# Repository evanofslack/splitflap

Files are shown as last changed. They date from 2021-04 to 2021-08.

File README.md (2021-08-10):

# DIY Split-Flap Display

This is a work in progress DIY [split-flap display](https://en.wikipedia.org/wiki/Split-flap_display). This is a fork of [scottbez1/splitflap](https://github.com/scottbez1/splitflap) where the display housing has been modified to be use 3D printed parts and acrylic panels with the goal of producing a more compact design. By enclosing the stepper motor within the flap housing, the overall footprint of a single unit is reduced. The acrylic panels fully enclose the internal components, leading to a clean and minimal appearance. 



<a href="https://www.youtube.com/watch?v=UAQJJAQSg_g" target="_blank">How a split-flap display works</a>

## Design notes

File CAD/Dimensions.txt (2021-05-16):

"Width"= 64mm

"Height" = 150mm

"Depth"= 90mm

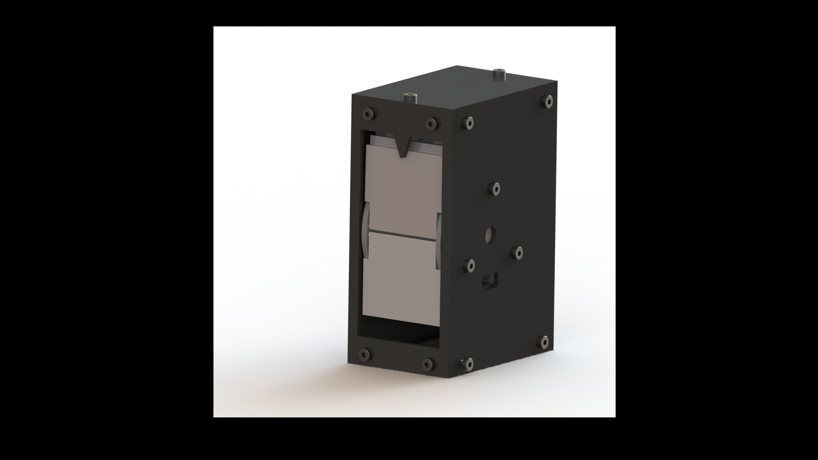
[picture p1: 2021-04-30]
renders/Render2.JPG

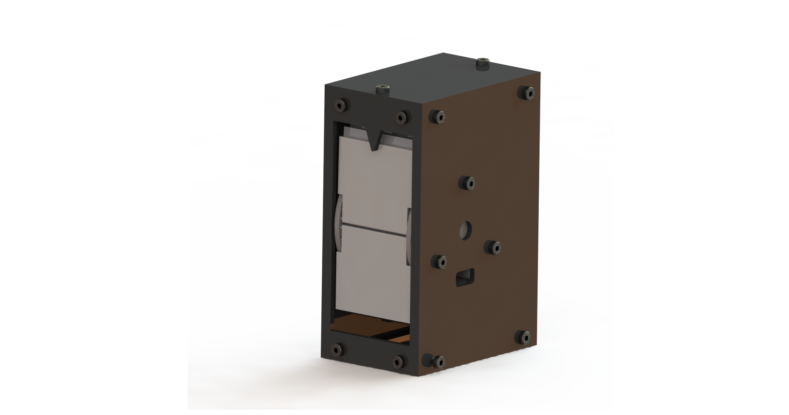
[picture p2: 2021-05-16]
renders/CollapsedRender.png

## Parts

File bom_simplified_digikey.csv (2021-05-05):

Quantity | Digi-Key Part Number | Customer Reference
2 | P5193-ND | C1, C3
1 | BC2665CT-ND | C2
1 | CP-202A-ND | CON1
1 | 732-5010-ND | D1
1 | 732-5008-ND | D2
1 | S1012EC-02-ND | JP1
1 | S9337-ND | JP1
4 | 455-2270-ND | P1, P2, P3, P4
3 | S1012EC-04-ND | P6, P7, P8
4 | S1112EC-03-ND | P100, P100, P100, P100
1 | CF14JT2K20CT-ND | R1
5 | CF14JT47K0CT-ND | R3, R4, R5, R6, R10
1 | CF14JT220RCT-ND | R7
1 | CF14JT470RCT-ND | R9
1 | S1012EC-03-ND | U1
1 | S1012EC-02-ND | U1
1 | S7106-ND | U1
2 | 576-1309-ND | U2, U4
1 | 296-8251-5-ND | U3
1 | 1528-1104-ND | U5, U6, U7, U8
4 | AH3391Q-P-BDI-ND | U100, U100, U100, U100
4 | 469-1027-ND | U100, U100, U100, U100

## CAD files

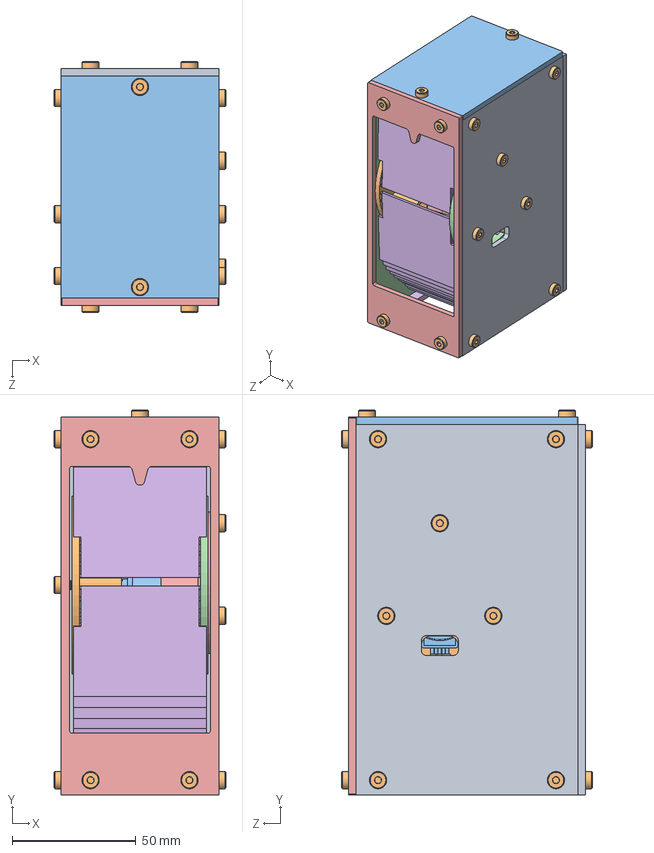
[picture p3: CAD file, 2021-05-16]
CAD/SplitFlapAssembly.SLDASM
69.6 x 155.8 x 101.6 mm
RightPanel
Holder1
Motor_28BYJ-48
Holder2
MotorHolder
Flap x 45
Hall Effect Sensor
LinkageV2
BackPanel
93070A101_LOW-PROFILE SOCKET HEAD CAP SCREW x 22
TopPanel
LeftPanel
FrontPanel
LinkageBottom

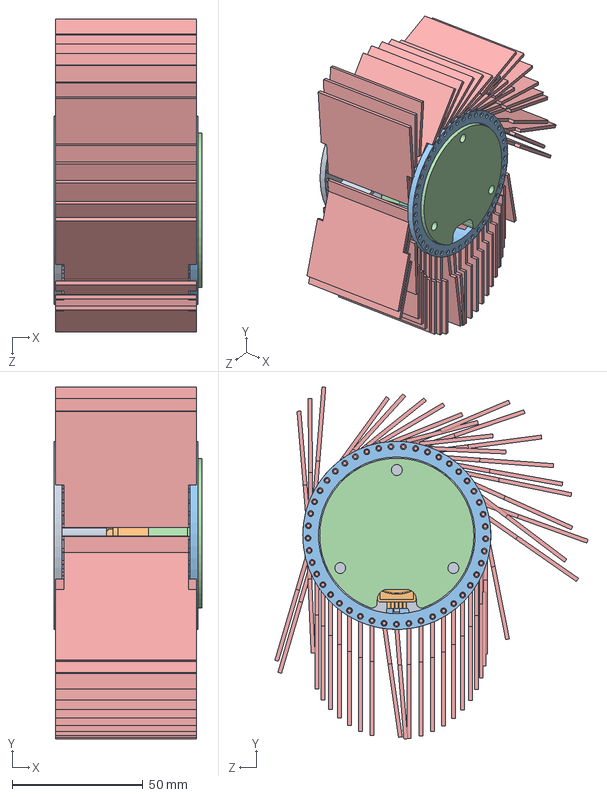
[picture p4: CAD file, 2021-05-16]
CAD/MotorAssembly.SLDASM
56.5 x 134.7 x 119.9 mm
Holder1
Motor_28BYJ-48
Holder2
MotorHolder
Flap x 45
Hall Effect Sensor

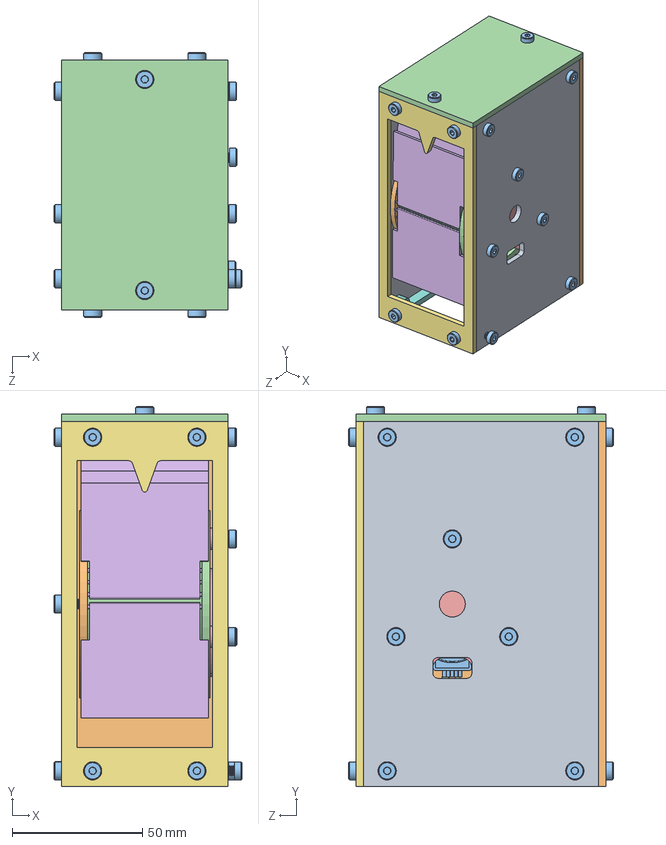
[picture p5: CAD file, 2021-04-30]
CAD/SplitFlapAssemblyExplode.SLDASM
72.1 x 145.8 x 101.6 mm
RightPanel
Holder1
Motor_28BYJ-48
Holder2
MotorHolder
Flap x 12
FrontPanel
LinkageV2 x 2
LeftPanel
BackPanel
93070A101_LOW-PROFILE SOCKET HEAD CAP SCREW x 22
TopPanel

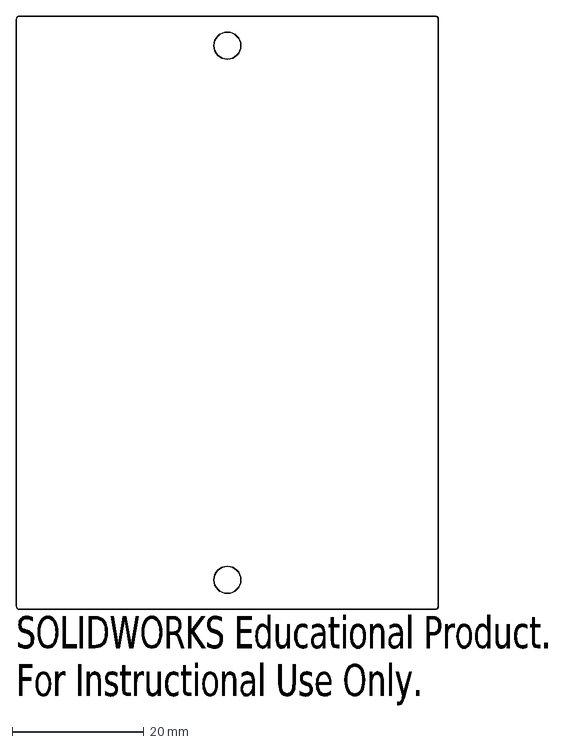
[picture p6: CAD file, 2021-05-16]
CAD/01_Acrylic/DXF/(4x)TopPanel.DXF
SOLIDWORKS Educational Product.
For Instructional Use Only.

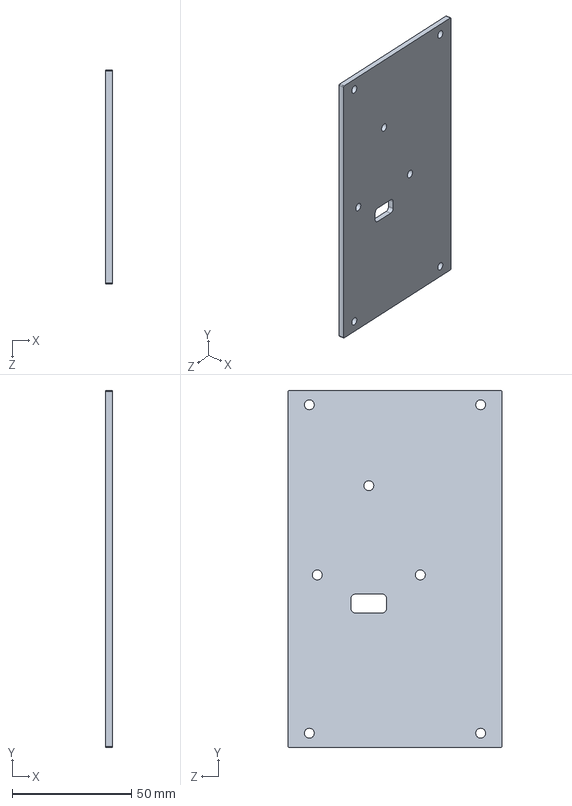
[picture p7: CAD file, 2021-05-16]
CAD/01_Acrylic/RightPanel.SLDPRT
3.00 x 150.0 x 90.0 mm

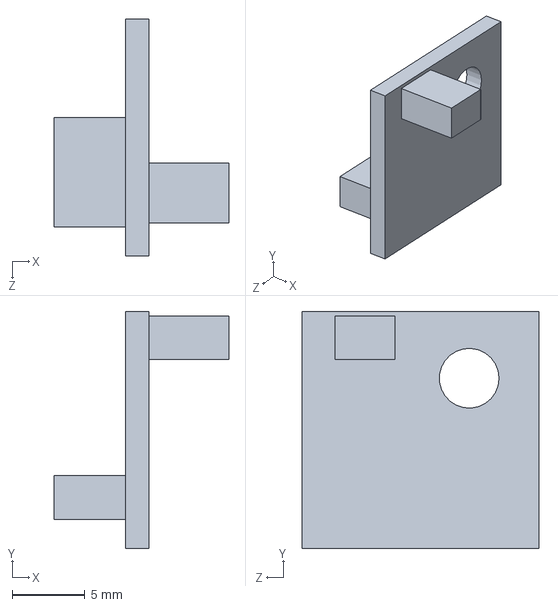
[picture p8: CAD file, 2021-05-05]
CAD/02_OTS/Hall Effect Sensor.SLDPRT
12.0 x 16.3 x 16.3 mm

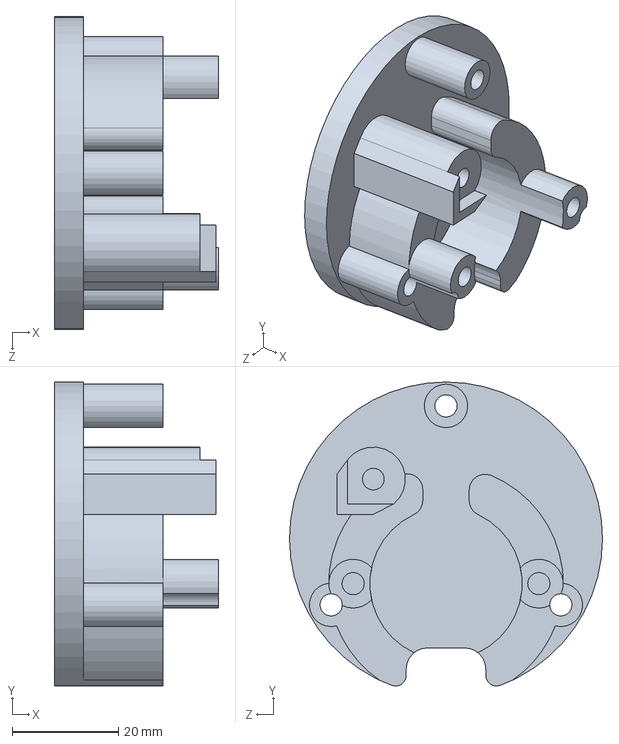
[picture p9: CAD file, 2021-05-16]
CAD/03_3DPrint/MotorHolder.SLDPRT
31.0 x 57.3 x 59.0 mm

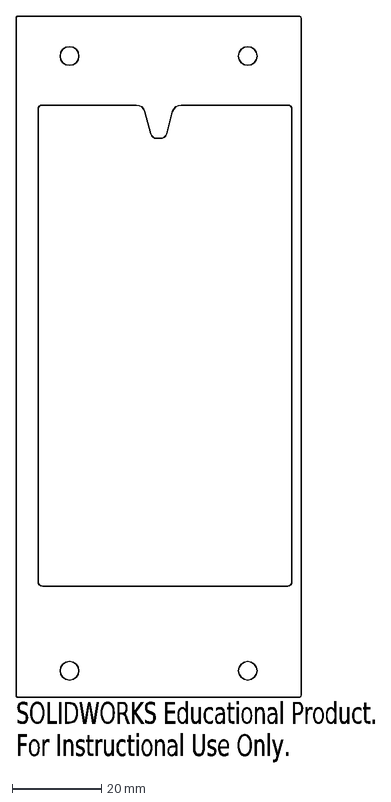
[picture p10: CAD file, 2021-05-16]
CAD/01_Acrylic/DXF/(3x)FrontPanel.DXF
SOLIDWORKS Educational Product.
For Instructional Use Only.

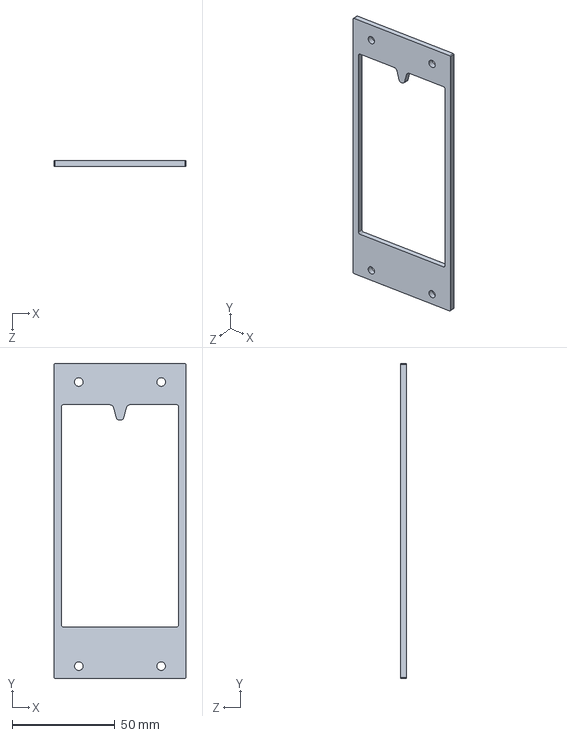
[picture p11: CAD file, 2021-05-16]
CAD/01_Acrylic/FrontPanel.SLDPRT
64.0 x 153.0 x 3.00 mm

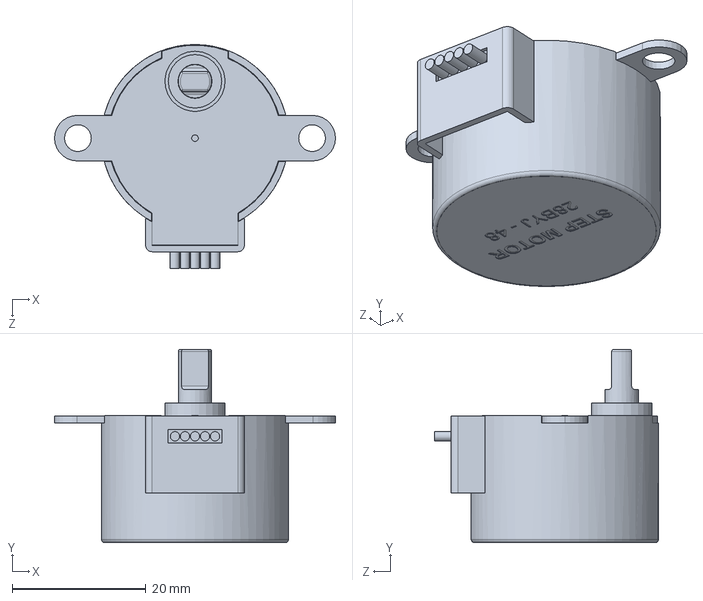
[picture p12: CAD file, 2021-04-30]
CAD/02_OTS/Motor_28BYJ-48.SLDPRT
42.0 x 28.9 x 33.5 mm

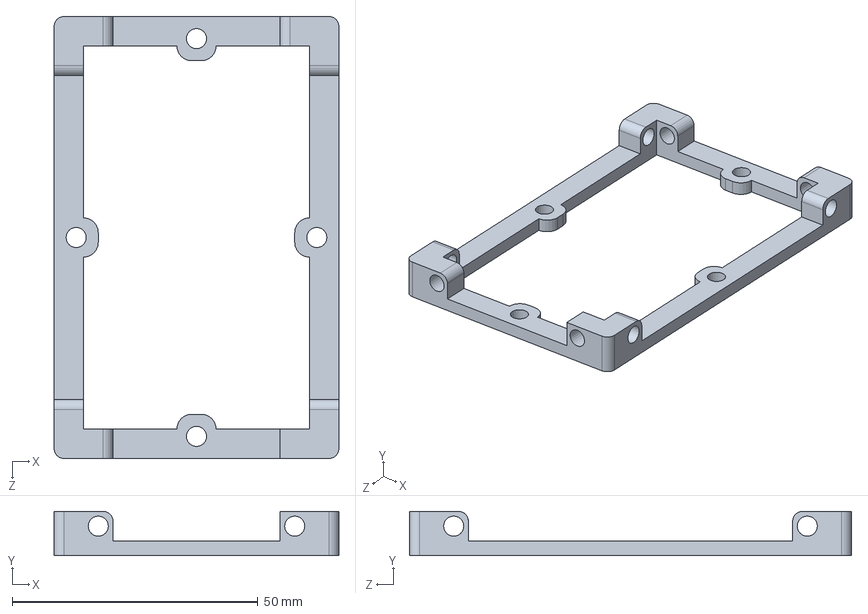
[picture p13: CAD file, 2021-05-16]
CAD/03_3DPrint/LinkageV2.SLDPRT
58.0 x 9.00 x 90.0 mm

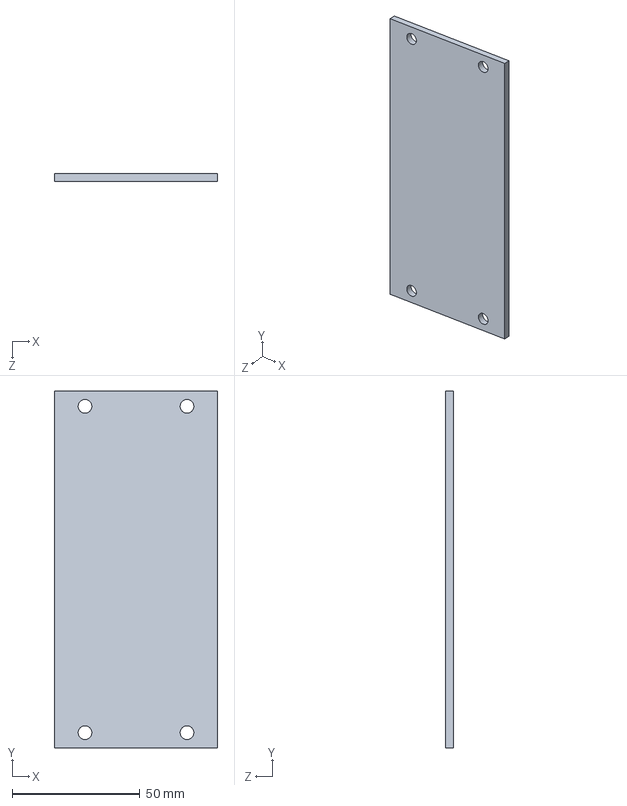
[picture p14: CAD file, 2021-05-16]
CAD/01_Acrylic/BackPanel.SLDPRT
64.0 x 140.0 x 3.00 mm

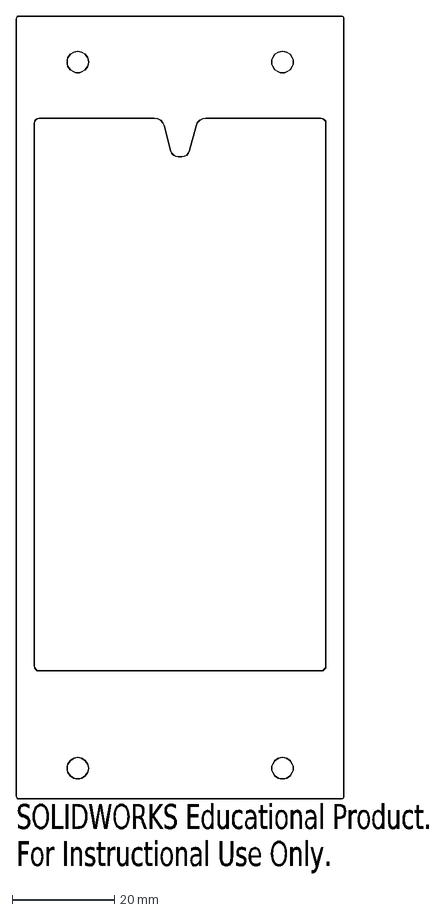
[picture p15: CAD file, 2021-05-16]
CAD/01_Acrylic/DXF/(4x)FrontPanel.DXF
SOLIDWORKS Educational Product.
For Instructional Use Only.

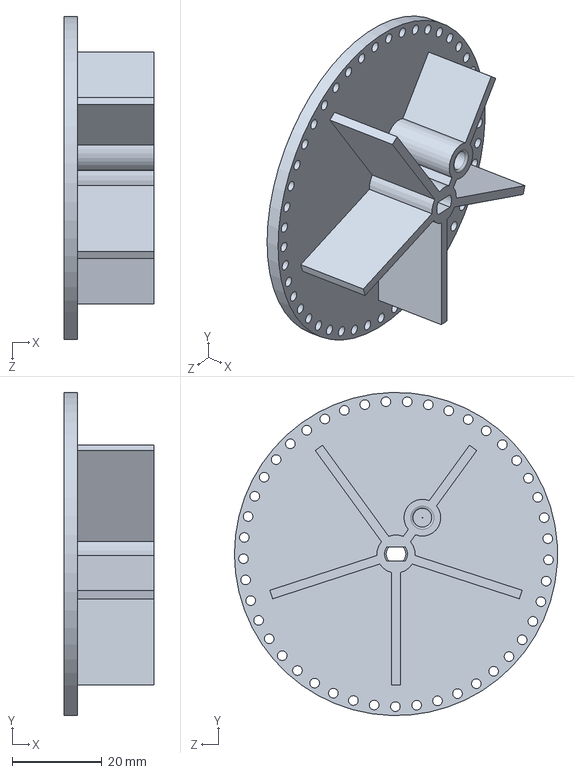
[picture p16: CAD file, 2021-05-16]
CAD/03_3DPrint/Holder1.SLDPRT
20.0 x 72.0 x 72.0 mm

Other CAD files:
CAD/01_Acrylic/DXF/(1x)LeftPanel.DXF
CAD/01_Acrylic/LeftPanel.SLDPRT
CAD/03_3DPrint/LinkageBottom.SLDPRT
CAD/01_Acrylic/DXF/(1x)RightPanel.DXF
CAD/01_Acrylic/DXF/FrontPanel.DXF
CAD/01_Acrylic/DXF/LeftPanel.DXF
CAD/01_Acrylic/DXF/RightPanel.DXF
CAD/01_Acrylic/LeftSidePanel.SLDPRT
CAD/02_OTS/93070A101_LOW-PROFILE SOCKET HEAD CAP SCREW.SLDPRT
CAD/03_3DPrint/Flap.SLDPRT
CAD/03_3DPrint/Flap.STL
CAD/03_3DPrint/FlapStopper.SLDPRT
CAD/03_3DPrint/Holder1.STL
CAD/03_3DPrint/Holder2-minimal.SLDPRT
CAD/03_3DPrint/Holder2-minimal.STL
CAD/03_3DPrint/Holder2.SLDPRT
CAD/03_3DPrint/Holder2.STL
CAD/03_3DPrint/InternalLinkage.SLDPRT
CAD/03_3DPrint/LinkageBottom.STL
CAD/03_3DPrint/LinkageV2.STL
CAD/03_3DPrint/MotorHolder.STL
CAD/03_3DPrint/TopPanel.SLDPRT

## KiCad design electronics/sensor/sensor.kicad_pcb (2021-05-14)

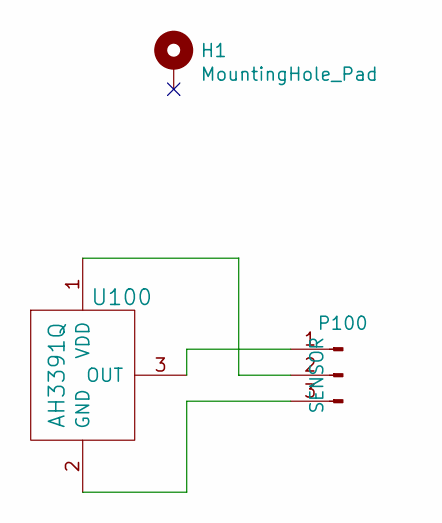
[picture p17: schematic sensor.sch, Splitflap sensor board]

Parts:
H1: MountingHole_Pad; M4_mount
P100: SENSOR; Pin_Header_Straight_1x03
U100: AH3391Q; hall_effect

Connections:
unnamed: P100.1, U100.3 (OUT)
unnamed: P100.2, U100.1 (VDD)
unnamed: P100.3, U100.2 (GND)

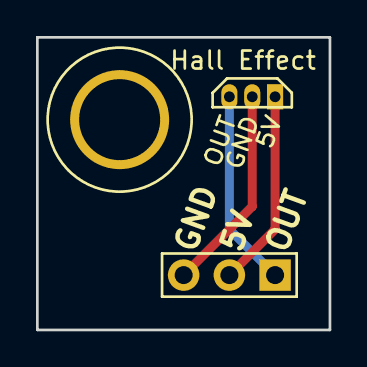
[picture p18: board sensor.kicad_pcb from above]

Board: 2 copper layers, 16.3 x 16.3 mm, 3 parts (1 on the bottom side), 3 nets.

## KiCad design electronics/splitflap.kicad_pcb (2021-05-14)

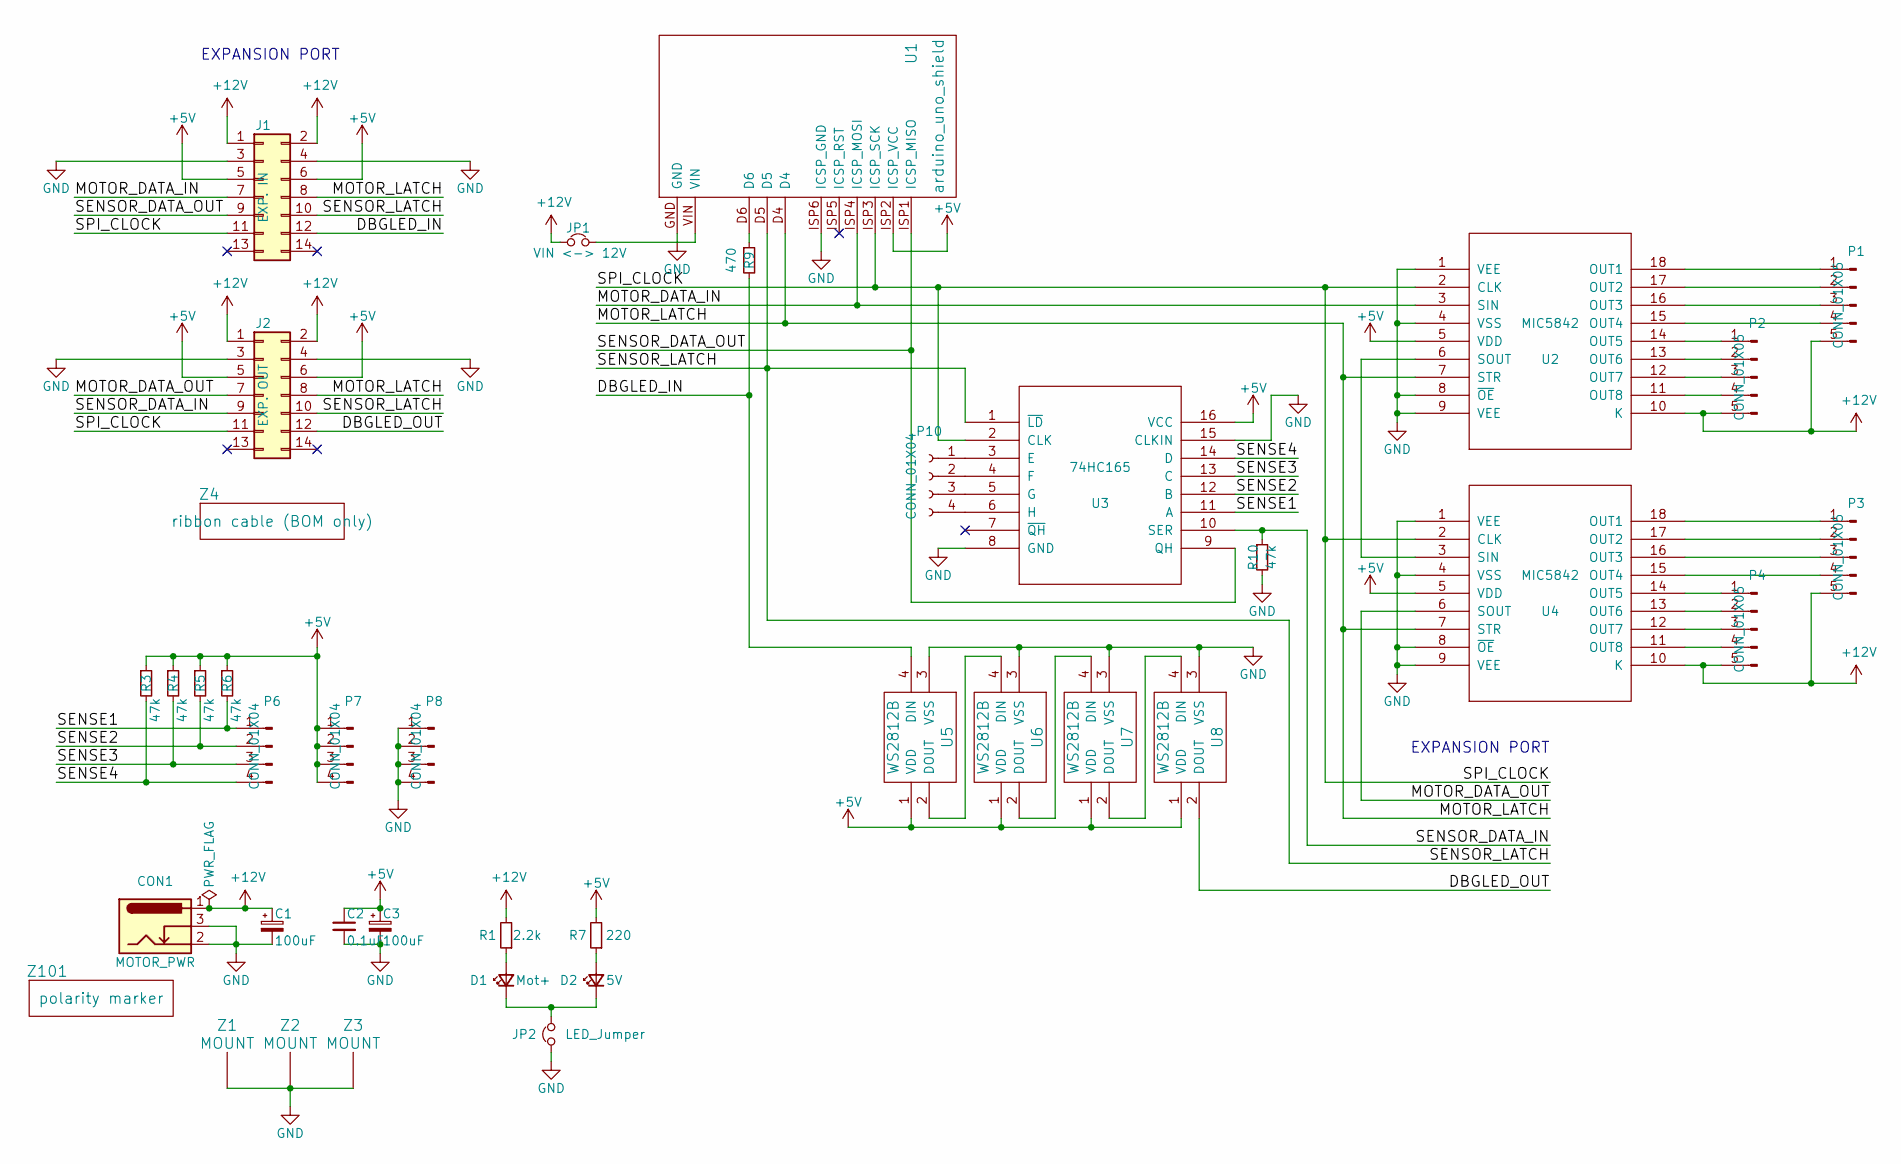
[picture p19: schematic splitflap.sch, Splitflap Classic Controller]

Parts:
C1, C3: 100uF; CP_Radial_D8.0mm_P3.50mm
C2: 0.1uF; C_Rect_L7.0mm_W2.5mm_P5.00mm
CON1: MOTOR_PWR; PJ-202A
D1: Mot+; LED_D3.0mm
D2: 5V; LED_D3.0mm
J1: EXP. IN; Pin_Header_Straight_2x07_Pitch2.54mm_IDC_Shrouded
J2: EXP. OUT; Pin_Header_Straight_2x07_Pitch2.54mm_IDC_Shrouded
JP1: VIN <-> 12V; Pin_Header_Straight_1x02_Pitch2.54mm
JP2: LED_Jumper; SolderJumper-2_P1.3mm_Bridged_Pad1.0x1.5mm
P1, P2, P3, P4: CONN_01X05; JST_XH_2-5mm_5pin
P6, P7, P8, P10: CONN_01X04; Pin_Header_Straight_1x04
R1: 2.2k; R_Axial_DIN0204_L3.6mm_D1.6mm_P7.62mm_Horizontal
R3, R4, R5, R6, R10: 47k; R_Axial_DIN0204_L3.6mm_D1.6mm_P7.62mm_Horizontal
R7: 220; R_Axial_DIN0204_L3.6mm_D1.6mm_P7.62mm_Horizontal
R9: 470; R_Axial_DIN0204_L3.6mm_D1.6mm_P7.62mm_Horizontal
U1: arduino_uno_shield
U2, U4: MIC5842; DIP-18_W7.62mm
U3: 74HC165; 74HC165_DIP-16_W7.62mm
U5, U6, U7, U8: WS2812B; LED_WS2812B_PLCC4_5.0x5.0mm_P3.2mm
Z1, Z2, Z3: MOUNT; M4_mount
Z4: ribbon cable (BOM only); Dummy_Empty
Z101: polarity marker; PolarityCenterPositive

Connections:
+5V: C2.1, C3.1, J1.5, J1.6, J2.5, J2.6, P7.1, P7.2, P7.3, P7.4, R3.1, R4.1, R5.1, R6.1, R7.2, U1.ISP2 (ICSP_VCC), U2.5 (VDD), U3.16 (VCC), U4.5 (VDD), U5.1 (VDD), U6.1 (VDD), U7.1 (VDD), U8.1 (VDD)
+12V: C1.1, CON1.1, J1.1, J1.2, J2.1, J2.2, JP1.1, P1.5, P2.5, P3.5, P4.5, R1.2, U2.10 (K), U4.10 (K)
/DBGLED_IN: J1.12, R9.2, U5.4 (DIN)
/DBGLED_OUT: J2.12, U8.2 (DOUT)
/MOTOR_DATA_IN: J1.7, U1.ISP4 (ICSP_MOSI), U2.3 (SIN)
/MOTOR_DATA_OUT: J2.7, U4.6 (SOUT)
/MOTOR_LATCH: J1.8, J2.8, U1.D4, U2.7 (STR), U4.7 (STR)
/SENSE1: P6.1, R6.2, U3.11 (A)
/SENSE2: P6.2, R5.2, U3.12 (B)
/SENSE3: P6.3, R4.2, U3.13 (C)
/SENSE4: P6.4, R3.2, U3.14 (D)
/SENSOR_DATA_IN: J2.9, R10.1, U3.10 (SER)
/SENSOR_DATA_OUT: J1.9, U1.ISP1 (ICSP_MISO), U3.9 (QH)
/SENSOR_LATCH: J1.10, J2.10, U1.D5, U3.1 (~LD)
/SPI_CLOCK: J1.11, J2.11, U1.ISP3 (ICSP_SCK), U2.2 (CLK), U3.2 (CLK), U4.2 (CLK)
unnamed: D1.1 (K), D2.1 (K), JP2.2
unnamed: D1.2 (A), R1.1
unnamed: D2.2 (A), R7.1
unnamed: P1.1, U2.18 (OUT1)
unnamed: P1.2, U2.17 (OUT2)
unnamed: P1.3, U2.16 (OUT3)
unnamed: P1.4, U2.15 (OUT4)
unnamed: P2.1, U2.14 (OUT5)
unnamed: P2.2, U2.13 (OUT6)
unnamed: P2.3, U2.12 (OUT7)
unnamed: P2.4, U2.11 (OUT8)
unnamed: P3.1, U4.18 (OUT1)
unnamed: P3.2, U4.17 (OUT2)
unnamed: P3.3, U4.16 (OUT3)
unnamed: P3.4, U4.15 (OUT4)
unnamed: P4.1, U4.14 (OUT5)
unnamed: P4.2, U4.13 (OUT6)
unnamed: P4.3, U4.12 (OUT7)
unnamed: P4.4, U4.11 (OUT8)
unnamed: P10.1, U3.3 (E)
unnamed: P10.2, U3.4 (F)
unnamed: P10.3, U3.5 (G)
unnamed: P10.4, U3.6 (H)
unnamed: R9.1, U1.D6
unnamed: U2.6 (SOUT), U4.3 (SIN)
unnamed: U5.2 (DOUT), U6.4 (DIN)
unnamed: U6.2 (DOUT), U7.4 (DIN)
unnamed: U7.2 (DOUT), U8.4 (DIN)

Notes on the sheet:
EXPANSION PORT

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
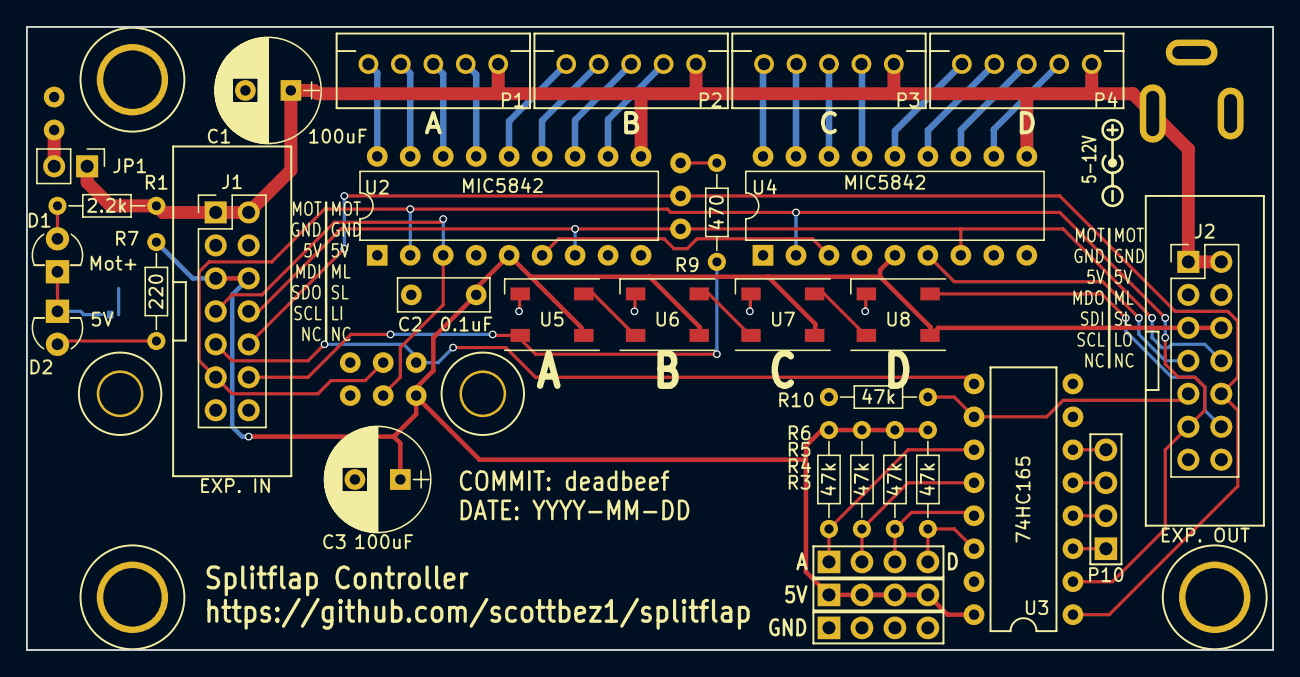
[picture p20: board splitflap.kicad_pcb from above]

Board: 2 copper layers, 96.0 x 48.0 mm, 39 parts (1 on the bottom side), 45 nets.

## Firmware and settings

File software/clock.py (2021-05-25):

# Evan Slack
# May 24 2021
#
# Set splitflap display to show current time
# Flash Arduino with main splitflap code then disconnect
# from serial and run this file from terminal

from splitflap import splitflap
from splitflap import ask_for_serial_port
from datetime import datetime
import time

def setTime():
    port = ask_for_serial_port()
    start = True
    print('Starting Clock...')
    with splitflap(port) as s:
        while True:
            currentTime = datetime.now()
            if start or currentTime.second == 0:
                start = False
                string = "{:02d}{:02d}".format(currentTime.hour, currentTime.minute)
                print('Going to {}'.format(string))
                status = s.set_text(string)
                s.print_status(status)
                time.sleep(1)

if __name__ == '__main__':
    setTime()

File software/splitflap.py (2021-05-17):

import json
from contextlib import contextmanager

import serial
import serial.tools.list_ports

import six

_ALPHABET = {
    ' ',
    'a', 'b', 'c', 'd', 'e', 'f', 'g', 'h', 'i', 'j', 'k', 'l', 'm',
    'n', 'o', 'p', 'q', 'r', 's', 't', 'u', 'v', 'w', 'x', 'y', 'z',
    '0', '1', '2', '3', '4', '5', '6', '7', '8', '9',
    '.', ',', '\'', '!', '#', '$', '%', '^'
}


class Splitflap(object):

    def __init__(self, serial_instance):
        self.serial = serial_instance

        self.has_inited = False
        self.num_modules = 0
        self.character_list = ""

        self.last_command = None
        self.last_status = None
        self.exception = None

    def _loop_for_status(self):
        while True:
            line = self.serial.readline().lstrip(b'\0').rstrip(b'\n')
            print(line)
            if not len(line):
                continue
            try:
                data = json.loads(line)
            except:
                print('Failed to parse', line)
                raise
            t = data['type']
            if t == 'init':
                if self.has_inited:
                    raise RuntimeError('Unexpected re-init!')
                self.has_inited = True
                self.num_modules = data['num_modules']
                try:
                    self.character_list = data['character_list']
                except KeyError:
                    self.character_list = _ALPHABET  # for compatibility

            elif t == 'move_echo':
                if not self.has_inited:
                    raise RuntimeError('Got move_echo before init!')
                if self.last_command is None:
                    raise RuntimeError('Unexpected move_echo response from controller')
                if self.last_command != data['dest']:
                    raise RuntimeError('Bad response from controller. Expected {!r} but got {!r}'.format(
                        self.last_command,
                        data['dest'],
                    ))
            elif t == 'status':
                if not self.has_inited:
                    raise RuntimeError('Got status before init!')
                if len(data['modules']) != self.num_modules:
                    raise RuntimeError('Wrong number of modules in status update. Expected {} but got {}'.format(
                        self.num_modules,
                        len(data['modules']),
                    ))
                self.last_status = data['modules']
                return self.last_status
            elif t == 'no_op':
                pass
            else:
                raise RuntimeError('Unexpected message: {!r}'.format(data))

    def in_character_list(self, letter):
        return letter in self.character_list

    def get_character_list(self):
        return self.character_list

    def set_text(self, text):
        text = text[0:self.num_modules]  # trim to number of modules available
        for letter in text:
            assert self.in_character_list(letter), 'Unexpected letter: {!r}. Must be one of {!r}'.format(
                letter,
                list(self.character_list),
            )
        self.last_command = text
        self.serial.write(b'=' + text.encode() + b'\n')
        return self._loop_for_status()

    def recalibrate_all(self):
        self.serial.write(b'@')
        return self._loop_for_status()

    def get_status(self):
        return self.last_status

    def get_num_modules(self):
        return self.num_modules

    def print_status(self, status=None):
        if(status is None):
            status = self.last_status

        for module in status:
            state = ''
            if module['state'] == 'panic':
                state = '!!!!'
            elif module['state'] == 'look_for_home':
                state = '...'
            elif module['state'] == 'sensor_error':
                state = '????'
            elif module['state'] == 'normal':
                state = module['flap']
            print('{:4}  {: 4} {: 4}'.format(state, module['count_missed_home'], module['count_unexpected_home']))


@contextmanager
def splitflap(serial_port):
    with serial.Serial(serial_port, 38400) as ser:
        s = Splitflap(ser)
        s._loop_for_status()
        yield s


def ask_for_serial_port():
    print('Available ports:')
    ports = sorted(
        filter(
            lambda p: p.description != 'n/a',
            serial.tools.list_ports.comports(),
        ),
        key=lambda p: p.device,
    )
    for i, port in enumerate(ports):
        print('[{: 2}] {} - {}'.format(i, port.device, port.description))
    print()
    value = six.moves.input('Use which port? ')
    port_index = int(value)
    assert 0 <= port_index < len(ports)
    return ports[port_index].device

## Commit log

2021-04-30 Added SolidWorks files and renders
    Removed original 3D models and populated with my own parts and assemblies
    [28byj-48.scad, 93070A101_LOW-PROFILE SOCKET HEAD CAP SCREW.SLDPRT, BackPanel.SLDPRT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]
2021-05-04 Updated motor housing
    Added Hall Effect Sensor PCB housing
2021-05-04 Added housing for Hall Effect Sensor PCB
    [FrontPanel.DXF, FrontPanel.SLDPRT, Hall Effect Sensor.SLDPRT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]
2021-05-05 Added Stepper Test Code
2021-05-05 Updated BOM
    [bom_simplified_digikey.csv]
2021-05-10 Added correct spin direction
    [StepperTest.ino]
2021-05-10 Tested motor
2021-05-13 change motor direction
2021-05-13 reverse motor direction
2021-05-16 Updated CAD model
    [(1x)LeftPanel.DXF, (1x)RightPanel.DXF, (3x)FrontPanel.DXF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]
2021-05-16 Added lasercut Illustrator files
2021-05-25 Revert "update clock file"
    This reverts commit a57bf8ddad6392e1a2bbd32d986516ab5ee9b13b.
    [clock.py, flap_test.py]
